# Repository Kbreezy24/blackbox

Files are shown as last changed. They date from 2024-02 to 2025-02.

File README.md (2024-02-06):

# Blackbox
Blackbox is an open source CoreXY tool-changing 3D Printer. Originally designed and open-sourced by Marc Schömann

Blackbox is a tool changing 3D Printer originally designed by Marc Schöemann to overcome the issue on properly integrating flexible materials with rigid materials for the production of flexible robotic appendages. The current revision of Blackbox was released as an open source project in 2017 and today we are happy to bring you the first of the Blackbox Family of tool changers - Blackbox CE (Community Edition). CE aims to accelerate the project through community participation and engagement via an accessible BOM and ease-of-assembly refinements.

# Is there a kit available for parts? 

Yes - Blackbox is supported by KB3D! Parts are available individually or as comprehensive kits. We continue to work with LDO Motors , Mandala Rose Works , and other trusted community vendors to expand your options.

# This machine looks intimidating, can I build one? 

Yes, but maybe. Blackbox has some new (to most) design elements that will push you to learn about systems you may not have dealt with before. In general though, the recommendations from other DIY printer build communities translate well. Those are typically as follows:<br />

This probably shouldn’t be your first 3D printer. There are always exceptions, but the experience you have will likely lean on your previously acquired skills from using and maintaining other machines. 
Despite our best efforts to guide you along, every machine will be different. From the quality of the printed parts to the nuances of your particular configuration. You should be comfortable with the fact that your attention to detail and where-with-all will determine the final product.
You will learn a ton, and probably pick up some new tools to make your life easier. Learning takes time, and so will your build. This is not an 8 hour build!

# Can I contribute, and how?
 
Absolutely! We encourage everyone to give back to the project however possible. Here are some ideas:

Sharing of modifications made to your machine that you think improve the experience or broaden the use case<br />
CAD optimization and contribution<br />
Bug fixes, error reporting, and feedback/suggestions<br />
Documentation refinement<br />
Help your peers where possible<br />
Purchasing parts through our official store at KB3D. 

# Features and Specs: 

# General: 
Blackbox is a fully open source design years in the making. Proven results over multiple iterations creates a solid foundation for a community driven machine limited only by our imaginations.

# Mechanical: 
Build Area = 300x300x275(Z)
Extremely Space efficient machine size vs build size when compared to other Tool Changers<br />
CoreXY Motion System = Intuitive belt routing with easy to use tensioning system.<br />
Belt Driven Z-Axis = Extremely fast belted Z axis with counterweight system.<br />
Tool-Changing = Up to 5 chassis mounted tools<br />
FDM = Up to 5 direct drive FDM tool heads with excellent positional accuracy via kinematic coupling. Support for multiple hot end configurations.<br />
Unique X-axis mounted extruder motor saves cost and complexity<br />
Silicone nozzle wiping and sealing<br />
Enclosure = Fully enclosed build volume (Hood Optional)<br />
REPRAP = Designed in the spirit of Reprap utilizing easily obtainable and 3D printable parts.<br />
Watercooling = Passive watercooling of all tools at all times in addition to a passively cooled extruder stepper<br />
Fully automated tool offset configuration using the late Danal Estes TAMV alignment system run from a Raspberry Pi.<br />
Heated Bed: Mains heated and ultra flat with options for embedded magnets

# Electronics: 
Wiring = Designed with clean and functional wiring in mind<br />
Duet 3 Electronics<br />
Automatic Bed Leveling and Z-Offset Calibration<br />
24V, 12V and 5V power sources for extreme flexibility<br />
Blackstop Hall Effect Sensors<br />
Tool lock position end stop - never drop a tool!

# Attributions:

Tool lock wedge plates are from the Jubilee Project https://github.com/machineagency/jubilee<br />
Heated Bed is from the Voron Project https://github.com/VoronDesign/Voron-2

All files are released according to the following license unless specified differently in the file or directory: CERN-OHL-W: https://ohwr.org/project/cernohl/wikis/Documents/CERN-OHL-version-2

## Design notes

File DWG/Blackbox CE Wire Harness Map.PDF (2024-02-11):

Main Harness Name | WIRE Name | Component A | Connector A | Component B | Connector B | Length Wire Gauge Color Marker Motion? Connector Name

Power Inlet
| Jumper - Line | Power Inlet | Female Spade | Power Switch | Female Spade | 8CM | 18 BLK | N
| Jumper - Neutral | Power Inlet | Female Spade | Power Switch | Female Spade | 8CM | 18 WHT | N
| Line Wire | Power Switch | Female Spade | 24V Power Supply | Fork | 20CM | 18 BLK | N
| Neutral Wire | Power Switch | Female Spade | 24V Power Supply | Fork | 20CM | 18 WHT | N
| Ground Wire | Power Inlet | Female Spade | 24V Power Supply | Fork | 20CM | 18 GN/YEL | N
Solid State Relay
| Line Wire (IN) | 24V Power Supply | Fork | SSR | Fork | 57CM | 18 BLK | N
| LINE Wire (LOAD) | SSR | Fork | Heated Bed WAGO | Bare Wire? | 86CM | 18 BLK | Y
| Trigger + | Duet 3 6HC | Molex LG Pin 2 of 2 | SSR IN + | Fork | 42CM | 24 RED | N | OUT_3
| Trigger - | Duet 3 6HC | Molex LG Pin 1 of 2 | SSR IN - | Fork | 42CM | 24 BLK | N | OUT_3

Heated Bed WAGOs
| Neutral 120V Wire | 24V Power Supply | Fork | Heated Bed WAGO | Bare Wire? | 133CM | 18 WHT | Y
| Bed Thermistor + | Duet 3 6HC | Molex KK Pin 2 of 2 | Heated Bed WAGO | Bare Wire? | 118CM | 24 RED | Y | TEMP_3
| Bed Thermistor - | Duet 3 6HC | Molex KK Pin 1 of 2 | Heated Bed WAGO | Bare Wire? | 118CM | 24 BLK | Y | TEMP_3

SexBolt Offset Switch
Switch S | Sexbolt Switch | JST-XH Pin 1 of 2 | Duet 3 6HC | Molex KK Pin 4 of 5 | 141CM | 24 GREEN | Y | IO_5
Switch - | Sexbolt Switch | JST-XH Pin 2 of 2 | Duet 3 6HC | Molex KK Pin 3 of 5 | 141CM | 24 BLK | Y | IO_5
12V DC Converter
| 24V IN + | 24V Power Supply | Fork | 12V Converter | Fork | 67CM | 18 RED | N
| 24V IN - | 24V Power Supply | Fork | 12V Converter | Fork | 67CM | 18 BLK | N

5V DC Converter
| 24V IN + | 24V Power Supply | Fork | 12V Converter | Fork | 74CM | 18 RED | N
| 24V IN - | 24V Power Supply | Fork | 12V Converter | Fork | 74CM | 18 BLK | N
| 5V Out + | 5V Converter | Fork | Duet 3 6HC | Molex KK PIN 3 of 3 | 60CM | 20 RED | N | 5V_EXT
| 5V OUT - | 5V Converter | Fork | Duet 3 6HC | Molex KK Pin 1 of 3 | 60CM | 20 BLK | N | 5V_EXT

Duet 3 6HC
| 24V IN + | 24V Power Supply | Fork | Duet 3 6HC | Fork | 91CM | 18 RED | N | POWER_IN
| 24V IN - | 24V Power Supply | Fork | Duet 3 6HC | Fork | 91CM | 18 BLACK | N | POWER_IN

Duet 3 3HC
| 24V IN + | Duet 3 6HC | Fork | Duet 3 3HC | Fork | 39CM | 18 RED | N | POWER_IN
| 24V IN - | Duet 3 6HC | Fork | Duet 3 3HC | Fork | 39CM | 18 BLACK | N | POWER_IN

Water Pump
| Radiator Fan + | Duet 3 6HC | Molex KK Pin 2 of 2 | 6020 Fan | Microfit Receptacle Pin 1 of 4 | 50CM | 24 RED | N | OUT_9
| Radiator Fan - | Duet 3 6HC | Molex KK Pin 1 of 2 | 6020 Fan | Microfit Receptacle Pin 2 of 4 | 50CM | 24 BLK | N | OUT_9
| 12V Out + | 12V Converter | Fork | Water Pump + | Microfit Receptacle Pin 3 of 4 | 86CM | 20 RED | N
| 12V OUT - | 12V Converter | Fork | Water Pump - | Microfit Receptacle Pin 4 of 4 | 86CM | 20 BLK | N

Display
| Display Data 1 | Duet 3 6HC | Molex KK Pin 1 of 5 | PanelDue | Molex KK Pin 1 of 4 | 62CM | 24 RED | N | IO_0
| Display Data 2 | Duet 3 6HC | Molex KK Pin 2 of 5 | PanelDue | Molex KK Pin 4 of 4 | 62CM | 24 GREEN | N | IO_0
| Display Data 3 | Duet 3 6HC | Molex KK Pin 3 of 5 | PanelDue | Molex KK Pin 2 of 4 | 62CM | 24 BLACK | N | IO_0
| Display Data 4 | Duet 3 6HC | Molex KK Pin 4 of 5 | PanelDue | Molex KK Pin 3 of 4 | 62CM | 24 BLUE | N | IO_0

Tool Docks
| Tool 0 Heater + | Duet 3 6HC | Molex LG Pin 2 of 2 | Tool Dock 0 | Microfit Receptacle Pin 4 of 4 | 136CM | 20 RED | N | OUT_1
| Tool 0 Heater - | Duet 3 6HC | Molex LG Pin 1 of 2 | Tool Dock 0 | Microfit Receptacle Pin 1 of 4 | 136CM | 20 BLACK | N | OUT_1
| Tool 0 Thermistor + | Duet 3 6HC | Molex KK Pin 1 of 2 | Tool Dock 0 | Microfit Receptacle Pin 2 of 4 | 136CM | 24 RED | N | TEMP_0
| Tool 0 Thermistor - | Duet 3 6HC | Molex KK Pin 2 of 2 | Tool Dock 0 | Microfit Receptacle Pin 3 of 4 | 136CM | 24 BLACK | N | TEMP_0
| Tool 1 Heater + | Duet 3 6HC | Molex LG Pin 2 of 2 | Tool Dock 1 | Microfit Receptacle Pin 4 of 4 | 141CM | 20 RED | N | OUT_2
| Tool 1 Heater - | Duet 3 6HC | Molex LG Pin 1 of 2 | Tool Dock 1 | Microfit Receptacle Pin 1 of 4 | 141CM | 20 BLACK | N | OUT_2
| Tool 1 Thermistor + | Duet 3 6HC | Molex KK Pin 1 of 2 | Tool Dock 1 | Microfit Receptacle Pin 2 of 4 | 141CM | 24 RED | N | TEMP_1
| Tool 1 Thermistor - | Duet 3 6HC | Molex KK Pin 2 of 2 | Tool Dock 1 | Microfit Receptacle Pin 3 of 4 | 141CM | 24 BLACK | N | TEMP_1
| Tool 2 Heater + | Duet 3 3HC | Molex LG Pin 2 of 2 | Tool Dock 2 | Microfit Receptacle Pin 4 of 4 | 131CM | 20 RED | N | OUT_0
| Tool 2 Heater - | Duet 3 3HC | Molex LG Pin 1 of 2 | Tool Dock 2 | Microfit Receptacle Pin 1 of 4 | 131CM | 20 BLACK | N | OUT_0
| Tool 2 Thermistor + | Duet 3 3HC | Molex KK Pin 1 of 2 | Tool Dock 2 | Microfit Receptacle Pin 2 of 4 | 131CM | 24 RED | N | TEMP_0
| Tool 2 Thermistor - | Duet 3 3HC | Molex KK Pin 2 of 2 | Tool Dock 2 | Microfit Receptacle Pin 3 of 4 | 131CM | 24 BLACK | N | TEMP_0
| Tool 3 Heater + | Duet 3 3HC | Molex LG Pin 2 of 2 | Tool Dock 3 | Microfit Receptacle Pin 4 of 4 | 136CM | 20 RED | N | OUT_1
| Tool 3 Heater - | Duet 3 3HC | Molex LG Pin 1 of 2 | Tool Dock 3 | Microfit Receptacle Pin 1 of 4 | 136CM | 20 BLACK | N | OUT_1
| Tool 3 Thermistor + | Duet 3 3HC | Molex KK Pin 1 of 2 | Tool Dock 3 | Microfit Receptacle Pin 2 of 4 | 136CM | 24 RED | N | TEMP_1
| Tool 3 Thermistor - | Duet 3 3HC | Molex KK Pin 2 of 2 | Tool Dock 3 | Microfit Receptacle Pin 3 of 4 | 136CM | 24 BLACK | N | TEMP_1
| Tool 4 Heater + | Duet 3 3HC | Molex LG Pin 2 of 2 | Tool Dock 4 | Microfit Receptacle Pin 4 of 4 | 141CM | 20 RED | N | OUT_2
| Tool 4 Heater - | Duet 3 3HC | Molex LG Pin 1 of 2 | Tool Dock 4 | Microfit Receptacle Pin 1 of 4 | 141CM | 20 BLACK | N | OUT_2
| Tool 4 Thermistor + | Duet 3 3HC | Molex KK Pin 1 of 2 | Tool Dock 4 | Microfit Receptacle Pin 2 of 4 | 141CM | 24 RED | N | TEMP_2
| Tool 4 Thermistor - | Duet 3 3HC | Molex KK Pin 2 of 2 | Tool Dock 4 | Microfit Receptacle Pin 3 of 4 | 141CM | 24 BLACK | N | TEMP_2
Enclosure Lighting | LED + (Stick1) | Duet 3 6HC | Molex KK Pin 2 of 2 | Light Stick 1 | JST XH Pin 2 of 2 | 144CM | 20 RED | N | OUT_8
| LED - (Stick1) | Duet 3 6HC | Molex KK Pin 1 of 2 | Light Stick 1 | JST XH Pin 1 of 2 | 144CM | 20 BLACK | N | OUT_8
| LED + (Stick2) | Light Stick 1 | JST XH Pin 2 of 2 | Light Stick 2 | JST XH Pin 2 of 2 | 16CM | 20 RED | N
| LED - (Stick2) | Light Stick 1 | JST XH Pin 1 of 2 | Light Stick 2 | JST XH Pin 1 of 2 | 16CM | 20 BLACK | N
| LED + (Stick3) | Light Stick 2 | JST XH Pin 2 of 2 | Light Stick 3 | JST XH Pin 2 of 2 | 16CM | 20 RED | N
| LED - (Stick3) | Light Stick 2 | JST XH Pin 1 of 2 | Light Stick 3 | JST XH Pin 1 of 2 | 16CM | 20 BLACK | N

FDM Tools

| Tool 0 Heater + | Tool Dock 0 | Microfit Receptacle Pin 4 of 4 | Tool Heater + | Microfit Receptacle Pin 1 of 2 | 70CM | 20 RED | Y
| Tool 0 Heater - | Tool Dock 0 | Microfit Receptacle Pin 1 of 4 | Tool Heater - | Microfit Receptacle Pin 2 of 2 | 70CM | 20 BLACK | Y
| Tool 0 Thermistor + | Tool Dock 0 | Microfit Receptacle Pin 2 of 4 | Tool Thermistor + | Microfit Receptacle Pin 1 of 2 | 72CM | 24 RED | Y
| Tool 0 Thermistor - | Tool Dock 0 | Microfit Receptacle Pin 3 of 4 | Tool Thermistor - | Microfit Receptacle Pin 2 of 2 | 72CM | 24 BLACK | Y

TOOL HEAD
| E Motor Pair 1 | Duet 3 6HC | Molex LG Pin 1 of 4 | Extruder Motor | JST PH Pin 1 of 6 | 256CM | 24 RED | Y | DRIVER_3

# BLACKBOX CE WIRE HARNESS MAP

E Motor Pair 1 | Duet 3 6HC | Molex LG Pin 2 of 4 | Extruder Motor | JST PH Pin 3 of 6 | 256CM | 24 BLUE | Y | DRIVER_3
E Motor Pair 2 | Duet 3 6HC | Molex LG Pin 3 of 4 | Extruder Motor | JST PH Pin 4 of 6 | 256CM | 24 GREEN | Y | DRIVER_3
E Motor Pair 2 | Duet 3 6HC | Molex LG Pin 4 of 4 | Extruder Motor | JST PH Pin 6 of 6 | 256CM | 24 BLACK | Y | DRIVER_3
T Motor Pair 1 | Duet 3 6HC | Molex LG Pin 1 of 4 | Tool Lock Motor | Microfit Connector Pin 1 of 4 | 256CM | 24 RED | Y | DRIVER_4
T Motor Pair 1 | Duet 3 6HC | Molex LG Pin 2 of 4 | Tool Lock Motor | Microfit Connector Pin 2 of 4 | 256CM | 24 BLUE | Y | DRIVER_4
T Motor Pair 2 | Duet 3 6HC | Molex LG Pin 3 of 4 | Tool Lock Motor | Microfit Connector Pin 3 of 4 | 256CM | 24 GREEN | Y | DRIVER_4
T Motor Pair 2 | Duet 3 6HC | Molex LG Pin 4 of 4 | Tool Lock Motor | Microfit Connector Pin 4 of 4 | 256CM | 24 BLACK | Y | DRIVER_4
X Endstop + | Duet 3 6HC | Molex KK Pin 5 of 5 | X Endstop | JST XH Pin 1 of 3 | 256CM | 24 RED | Y | IO_1
X Endstop S | Duet 3 6HC | Molex KK Pin 4 of 5 | X Endstop | JST XH Pin 2 of 3 | 256CM | 24 GREEN | Y | IO_1
X Endstop - | Duet 3 6HC | Molex KK Pin 3 of 5 | X Endstop | JST XH Pin 3 of 3 | 256CM | 24 BLACK | Y | IO_1
Z Endstop S | Duet 3 6HC | Molex KK Pin 4 of 5 | Z Endstop | Microfit Connector Pin 1 of 2 | 256CM | 24 GREEN | Y | IO_3
Z Endstop - | Duet 3 6HC | Molex KK Pin 3 of 5 | Z Endstop | Microfit Connector Pin 2 of 2 | 256CM | 24 BLACK | Y | IO_3
TL Endstop + | Duet 3 6HC | Molex KK Pin 5 of 5 | Tool Lock Endstop | JST XH Pin 1 of 3 | 256CM | 24 RED | Y | IO_4
TL Endstop S | Duet 3 6HC | Molex KK Pin 4 of 5 | Tool Lock Endstop | JST XH Pin 2 of 3 | 256CM | 24 GREEN | Y | IO_4
TL Endstop - | Duet 3 6HC | Molex KK Pin 3 of 5 | Tool Lock Endstop | JST XH Pin 3 of 3 | 256CM | 24 BLACK | Y | IO_4
Part Fan + | Duet 3 6HC | Molex KK Pin 2 of 2 | Part cooling Fan | Microfit Connector Pin 1 of 2 | 256CM | 24 RED | Y | OUT_7
Part Fan - | Duet 3 6HC | Molex KK Pin 1 of 2 | Part cooling Fan | Microfit Connector Pin 2 of 2 | 256CM | 24 BLACK | Y | OUT_7

Y Endstop

Y Endstop + | Duet 3 6HC | Molex KK Pin 5 of 5 | Y Endstop | JST XH Pin 1 of 3 | 83CM | 24 RED | N | IO_2
Y Endstop S | Duet 3 6HC | Molex KK Pin 4 of 5 | Y Endstop | JST XH Pin 2 of 3 | 83CM | 24 GREEN | N | IO_2
Y Endstop - | Duet 3 6HC | Molex KK Pin 3 of 5 | Y Endstop | JST XH Pin 3 of 3 | 83CM | 24 BLACK | N | IO_2

B Motor
B Motor Pair 1 | Duet 3 6HC | Molex LG Pin 1 of 4 | B Motor | JST PH Pin 1 of 6 | 61CM | 24 RED | N | DRIVER_0
B Motor Pair 1 | Duet 3 6HC | Molex LG Pin 2 of 4 | B Motor | JST PH Pin 3 of 6 | 61CM | 24 BLUE | N | DRIVER_0
B Motor Pair 2 | Duet 3 6HC | Molex LG Pin 3 of 4 | B Motor | JST PH Pin 4 of 6 | 61CM | 24 GREEN | N | DRIVER_0
B Motor Pair 2 | Duet 3 6HC | Molex LG Pin 4 of 4 | B Motor | JST PH Pin 6 of 6 | 61CM | 24 BLACK | N | DRIVER_0

A Motor
A Motor Pair 1 | Duet 3 6HC | Molex LG Pin 1 of 4 | A Motor | JST PH Pin 1 of 6 | 173CM | 24 RED | N | DRIVER_1
A Motor Pair 1 | Duet 3 6HC | Molex LG Pin 2 of 4 | A Motor | JST PH Pin 3 of 6 | 173CM | 24 BLUE | N | DRIVER_1
A Motor Pair 2 | Duet 3 6HC | Molex LG Pin 3 of 4 | A Motor | JST PH Pin 4 of 6 | 173CM | 24 GREEN | N | DRIVER_1
A Motor Pair 2 | Duet 3 6HC | Molex LG Pin 4 of 4 | A Motor | JST PH Pin 6 of 6 | 173CM | 24 BLACK | N | DRIVER_1

Z Motor
Z Motor Pair 1 | Duet 3 6HC | Molex LG Pin 1 of 4 | Z Motor | JST PH Pin 1 of 6 | 17CM | 24 RED | N | DRIVER_2
Z Motor Pair 1 | Duet 3 6HC | Molex LG Pin 2 of 4 | Z Motor | JST PH Pin 3 of 6 | 17CM | 24 BLUE | N | DRIVER_2
Z Motor Pair 2 | Duet 3 6HC | Molex LG Pin 3 of 4 | Z Motor | JST PH Pin 4 of 6 | 17CM | 24 GREEN | N | DRIVER_2
Z Motor Pair 2 | Duet 3 6HC | Molex LG Pin 4 of 4 | Z Motor | JST PH Pin 6 of 6 | 17CM | 24 BLACK | N | DRIVER_2

Raspberry Pi
RPI 5V+ | 5V DC Converter | Fork | RPI | USB-C | 40CM | 20 RED | N
RPI 5V- | 5V DC Converter | Fork | RPI | USB-C | 40CM | 20 BLK | N

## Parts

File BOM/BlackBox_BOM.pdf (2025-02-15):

# Blackbox BOM Export - CE - 08/18/2024

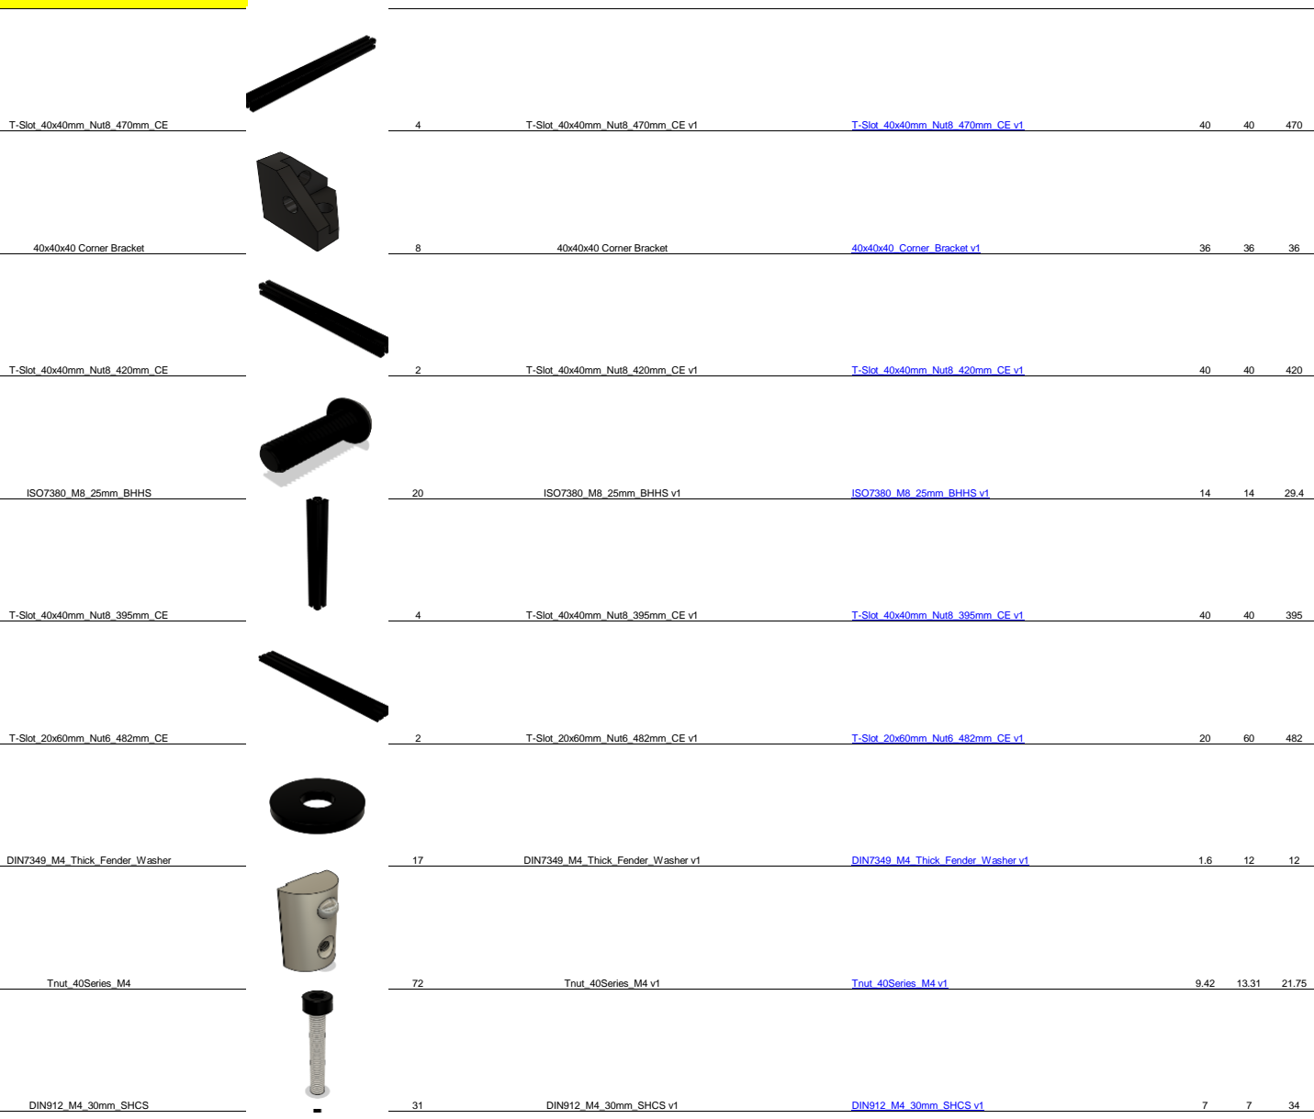
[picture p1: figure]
T-Slot_40x40mm_Nut8_470mm_CE; T-Slot_40x40mm_Nut8_470mm_CE v1; 40x40x40 Corner Bracket; 40x40x40_Corner_Bracket v1; T-Slot_40x40mm_Nut8_420mm_CE; T-Slot_40x40mm_Nut8_420mm_CE v1; ISO7380_M8_25mm_BHHS; ISO7380_M8_25mm_BHHS v1; T-Slot_40x40mm_Nut8_395mm_CE; T-Slot_40x40mm_Nut8_395mm_CE v1; T-Slot_20x60mm_Nut6_482mm_CE; T-Slot_20x60mm_Nut6_482mm_CE v1; DIN7349_M4_Thick_Fender_Washer; DIN7349_M4_Thick_Fender_Washer v1; Tnut_40Series_M4; Tnut_40Series_M4 v1; DIN912_M4_30mm_SHCS; DIN912_M4_30mm_SHCS v1

LinearRail_MGN12_335mm_LDO | 3 | LinearRail_MGN12_335mm_LDO v1 | LinearRail_MGN12_335mm_LDO v1 (https://gmail2024038.autodesk360.com/g/projects/20231224713178051/data/dXJuOmFkc2sud2lwcHJvZDpmcy5mb2xkZXI6Y28uMGxIVWluVGVSWTZtS2JGWFVKeEJkZw==/dXJuOmFkc2sud2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) | 8 | 12 | 335
Tnut_40Series_M3 | 36 | Tnut_40Series_M3 v1 | Tnut_40Series_M3 v1 (https://gmail2024038.autodesk360.com/g/projects/20231224713178051/data/dXJuOmFkc2sud2lwcHJvZDpmcy5mb2xkZXI6Y28uTktyRXlNMm5UcXFDbTlDbkJDRjZGQQ==/dXJuOmFkc2sud2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) | 9.42 | 13.31 | 21.75
DIN912_M3_14mm_SHCS | 44 | DIN912_M3_14mm_SHCS v1 | DIN912_M3_14mm_SHCS v1 (https://gmail2024038.autodesk360.com/g/projects/20231224713178051/data/dXJuOmFkc2sud2lwcHJvZDpmcy5mb2xkZXI6Y28uTktyRXlNMm5UcXFDbTlDbkJDRjZGQQ==/dXJuOmFkc2sud2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) | 5.5 | 5.5 | 17
LinearRail_MGN12_400mm_LDO | 2 | LinearRail_MGN12_400mm_LDO v1 | LinearRail_MGN12_400mm_LDO v1 (https://gmail2024038.autodesk360.com/g/projects/20231224713178051/data/dXJuOmFkc2sud2lwcHJvZDpmcy5mb2xkZXI6Y28uMGxIVWluVGVSWTZtS2JGWFVKeEJkZw==/dXJuOmFkc2sud2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) | 8 | 12 | 400
T-Slot_20x20mm_Nut6_395mm_CE | 1 | T-Slot_20x20mm_Nut6_395mm_CE v1 | T-Slot_20x20mm_Nut6_395mm_CE v1 (https://gmail2024038.autodesk360.com/g/projects/20231224713178051/data/dXJuOmFkc2sud2lwcHJvZDpmcy5mb2xkZXI6Y28uMGxIVWluVGVSWTZtS2JGWFVKeEJkZw==/dXJuOmFkc2sud2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) | 20 | 20 | 395
M4 20 Series T-Nut | 71 | M4 20 Series T-Nut | Tnut_20Series_M4 v1 (https://gmail2024038.autodesk360.com/g/projects/20231224713178051/data/dXJuOmFkc2sud2lwcHJvZDpmcy5mb2xkZXI6Y28uTktyRXlNMm5UcXFDbTlDbkJDRjZGQQ==/dXJuOmFkc2sud2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) | 4.3 | 7.709 | 12
DIN912_M4_16mm_SHCS | 6 | DIN912_M4_16mm_SHCS v1 | DIN912_M4_16mm_SHCS v1 (https://gmail2024038.autodesk360.com/g/projects/20231224713178051/data/dXJuOmFkc2sud2lwcHJvZDpmcy5mb2xkZXI6Y28uTktyRXlNMm5UcXFDbTlDbkJDRjZGQQ==/dXJuOmFkc2sud2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) | 7 | 7 | 20
DIN912_M4_35mm_SHCS | 14 | DIN912_M4_35mm_SHCS v1 | DIN912_M4_35mm_SHCS v1 (https://gmail2024038.autodesk360.com/g/projects/20231224713178051/data/dXJuOmFkc2sud2lwcHJvZDpmcy5mb2xkZXI6Y28uTktyRXlNMm5UcXFDbTlDbkJDRjZGQQ==/dXJuOmFkc2sud2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) | 7 | 7 | 39
M3 20 Series Roll-in Nut | 31 | M3 20 Series Roll-in Nut | Tnut_20Series_M3 v1 (https://gmail2024038.autodesk360.com/g/projects/20231224713178051/data/dXJuOmFkc2sud2lwcHJvZDpmcy5mb2xkZXI6Y28uTktyRXlNMm5UcXFDbTlDbkJDRjZGQQ==/dXJuOmFkc2sud2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) | 4.3 | 7.709 | 12

DIN912_M3_8mm_SHCS | 47 | DIN912_M3_8mm_SHCS v1 | DIN912_M3_8mm_SHCS v1 (https://gmail2024038.autodesk360.com/g/projects/20231224713178051/data/dXJuOmFkc2sud2lwcHJvZDpmcy5mb2xkZXI6Y28uTktyRXlNMm5UcXFDbTlDbkJDRjZGQQ==/dXJuOmFkc2sud2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) | 5.5 | 5.5 | 11
M3_4.6x4mm_Heat_Set_Insert | 173 | M3_4.6x4mm_Heat_Set_Insert v1 | M3_4.6x4mm_Heat_Set_Insert v1 (https://gmail2024038.autodesk360.com/g/projects/20231224713178051/data/dXJuOmFkc2sud2lwcHJvZDpmcy5mb2xkZXI6Y28uTktyRXlNMm5UcXFDbTlDbkJDRjZGQQ==/dXJuOmFkc2sud2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) | 4.3 | 4.7 | 4.7
DIN912_M3_10mm_SHCS | 36 | DIN912_M3_10mm_SHCS v1 | DIN912_M3_10mm_SHCS v1 (https://gmail2024038.autodesk360.com/g/projects/20231224713178051/data/dXJuOmFkc2sud2lwcHJvZDpmcy5mb2xkZXI6Y28uTktyRXlNMm5UcXFDbTlDbkJDRjZGQQ==/dXJuOmFkc2sud2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) | 5.5 | 5.5 | 13
M4_6x5mm_Heat_Set_Insert | 59 | M4_6x5mm_Heat_Set_Insert v1 | M4_6x5mm_Heat_Set_Insert v1 (https://gmail2024038.autodesk360.com/g/projects/20231224713178051/data/dXJuOmFkc2sud2lwcHJvZDpmcy5mb2xkZXI6Y28uTktyRXlNMm5UcXFDbTlDbkJDRjZGQQ==/dXJuOmFkc2sud2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) | 4.7 | 6.3 | 6.3
DIN7991_M4_25mm_FHHS | 8 | DIN7991_M4_25mm_FHHS v1 | DIN7991_M4_25mm_FHHS v1 (https://gmail2024038.autodesk360.com/g/projects/20231224713178051/data/dXJuOmFkc2sud2lwcHJvZDpmcy5mb2xkZXI6Y28uTktyRXlNMm5UcXFDbTlDbkJDRjZGQQ==/dXJuOmFkc2sud2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) | 8 | 8 | 25
Bearing_Flanged_5x10x4mm | 4 | Bearing_Flanged_5x10x4mm v1 | Bearing_Flanged_5x10x4mm v1 (https://gmail2024038.autodesk360.com/g/projects/20231224713178051/data/dXJuOmFkc2sud2lwcHJvZDpmcy5mb2xkZXI6Y28uMGxIVWluVGVSWTZtS2JGWFVKeEJkZw==/dXJuOmFkc2sud2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) | 4 | 11.6 | 11.6
GT2_40t_Pulley_9mm_Belt_5mm_Bore_Powge | 1 | GT2_40t_Pulley_9mm_Belt_5mm_Bore_Powge v1 | GT2_40t_Pulley_9mm_Belt_5mm_Bore_Powge v1 (https://gmail2024038.autodesk360.com/g/projects/20231224713178051/data/dXJuOmFkc2sud2lwcHJvZDpmcy5mb2xkZXI6Y28uMGxIVWluVGVSWTZtS2JGWFVKeEJkZw==/dXJuOmFkc2sud2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) | 23 | 30 | 30
GT2_16t_Pulley_9mm_Belt_5mm_Bore_Powge | 2 | GT2_16t_Pulley_9mm_Belt_5mm_Bore_Powge v1 | GT2_16t_Pulley_9mm_Belt_5mm_Bore_Powge v1 (https://gmail2024038.autodesk360.com/g/projects/20231224713178051/data/dXJuOmFkc2sud2lwcHJvZDpmcy5mb2xkZXI6Y28uMGxIVWluVGVSWTZtS2JGWFVKeEJkZw==/dXJuOmFkc2sud2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) | 14 | 14 | 21
Linear_Shaft_5x70mm | 1 | Linear_Shaft_5x70mm v1 | Linear_Shaft_5x70mm v1 (https://gmail2024038.autodesk360.com/g/projects/20231224713178051/data/dXJuOmFkc2sud2lwcHJvZDpmcy5mb2xkZXI6Y28uMGxIVWluVGVSWTZtS2JGWFVKeEJkZw==/dXJuOmFkc2sud2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) | 5 | 5 | 70

DIN916_M4_4mm_Set_Screw | 12 | DIN916_M4_4mm_Set_Screw v1 | DIN916_M4_4mm_Set_Screw v1 (https://gmail2024038.autodesk360.com/g/projects/20231224713178051/data/dXJuOmFkc2sud2lwcHJvZDpmcy5mb2xkZXI6Y28uTktyRXlNMm5UcXFDbTlDbkJDRjZGQQ==/dXJuOmFkc2sud2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) | 4 | 4 | 4.025
DIN916_M4_6mm_Set_Screw | 2 | DIN916_M4_6mm_Set_Screw v1 | DIN916_M4_6mm_Set_Screw v1 (https://gmail2024038.autodesk360.com/g/projects/20231224713178051/data/dXJuOmFkc2sud2lwcHJvZDpmcy5mb2xkZXI6Y28uTktyRXlNMm5UcXFDbTlDbkJDRjZGQQ==/dXJuOmFkc2sud2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) | 4 | 4.025 | 6
DIN912_M4_20mm_SHCS | 9 | DIN912_M4_20mm_SHCS v1 | DIN912_M4_20mm_SHCS v1 (https://gmail2024038.autodesk360.com/g/projects/20231224713178051/data/dXJuOmFkc2sud2lwcHJvZDpmcy5mb2xkZXI6Y28uTktyRXlNMm5UcXFDbTlDbkJDRjZGQQ==/dXJuOmFkc2sud2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) | 7 | 7 | 24
DIN912_M4_22mm_SHCS | 2 | DIN912_M4_22mm_SHCS v1 | DIN912_M4_22mm_SHCS v1 (https://gmail2024038.autodesk360.com/g/projects/20231224713178051/data/dXJuOmFkc2sud2lwcHJvZDpmcy5mb2xkZXI6Y28uTktyRXlNMm5UcXFDbTlDbkJDRjZGQQ==/dXJuOmFkc2sud2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) | 7 | 7 | 26
DIN912_M4_14mm_SHCS | 13 | DIN912_M4_14mm_SHCS v1 | DIN912_M4_14mm_SHCS v1 (https://gmail2024038.autodesk360.com/g/projects/20231224713178051/data/dXJuOmFkc2sud2lwcHJvZDpmcy5mb2xkZXI6Y28uTktyRXlNMm5UcXFDbTlDbkJDRjZGQQ==/dXJuOmFkc2sud2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) | 7 | 7 | 18
GT2_77t_Belt_9x154mm | 1 | GT2_77t_Belt_9x154mm v1 | GT2_77t_Belt_9x154mm v1 (https://gmail2024038.autodesk360.com/g/projects/20231224713178051/data/dXJuOmFkc2sud2lwcHJvZDpmcy5mb2xkZXI6Y28uMGxIVWluVGVSWTZtS2JGWFVKeEJkZw==/dXJuOmFkc2sud2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) | 9 | 26.217 | 66.973
Nema17_47mm | 3 | Nema17_47mm v1 | Nema17_47mm v1 (https://gmail2024038.autodesk360.com/g/projects/20231224713178051/data/dXJuOmFkc2sud2lwcHJvZDpmcy5mb2xkZXI6Y28uMGxIVWluVGVSWTZtS2JGWFVKeEJkZw==/dXJuOmFkc2sud2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) | 42 | 42 | 71.5
DIN912_M4_10mm_SHCS | 11 | DIN912_M4_10mm_SHCS v1 | DIN912_M4_10mm_SHCS v1 (https://gmail2024038.autodesk360.com/g/projects/20231224713178051/data/dXJuOmFkc2sud2lwcHJvZDpmcy5mb2xkZXI6Y28uTktyRXlNMm5UcXFDbTlDbkJDRjZGQQ==/dXJuOmFkc2sud2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) | 7 | 7 | 14
DIN912_M4_12mm_SHCS | 24 | DIN912_M4_12mm_SHCS v1 | DIN912_M4_12mm_SHCS v1 (https://gmail2024038.autodesk360.com/g/projects/20231224713178051/data/dXJuOmFkc2sud2lwcHJvZDpmcy5mb2xkZXI6Y28uTktyRXlNMm5UcXFDbTlDbkJDRjZGQQ==/dXJuOmFkc2sud2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) | 7 | 7 | 16

GT2_94t_Belt_9x188mm | 1 | GT2_94t_Belt_9x188mm v1 | GT2_94t_Belt_9x188mm v1 (https://gmail2024038.autodesk360.com/g/projects/20231224713178051/data/dXJuOmFkc2sud2lwcHJvZDpmcy5mb2xkZXI6Y28uMGxIVWluVGVSWTZtS2JGWFVKeEJkZw==/dXJuOmFkc2sud2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) | 9 | 51.682 | 72.109
GT2_80t_Pulley_9mm_Belt_8mm_Bore_Powge | 1 | GT2_80t_Pulley_9mm_Belt_8mm_Bore_Powge v1 | GT2_80t_Pulley_9mm_Belt_8mm_Bore_Powge v1 (https://gmail2024038.autodesk360.com/g/projects/20231224713178051/data/dXJuOmFkc2sud2lwcHJvZDpmcy5mb2xkZXI6Y28uMGxIVWluVGVSWTZtS2JGWFVKeEJkZw==/dXJuOmFkc2sud2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) | 23 | 54 | 54
DIN916_M5_12mm_Set_Screw | 2 | DIN916_M5_12mm_Set_Screw v1 | DIN916_M5_12mm_Set_Screw v1 (https://gmail2024038.autodesk360.com/g/projects/20231224713178051/data/dXJuOmFkc2sud2lwcHJvZDpmcy5mb2xkZXI6Y28uTktyRXlNMm5UcXFDbTlDbkJDRjZGQQ==/dXJuOmFkc2sud2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) | 5 | 5.025 | 12
T-Slot_10x20mm_Nut6_350mm_CE | 1 | T-Slot_10x20mm_Nut6_350mm_CE v1 | T-Slot_10x20mm_Nut6_350mm_CE v1 (https://gmail2024038.autodesk360.com/g/projects/20231224713178051/data/dXJuOmFkc2sud2lwcHJvZDpmcy5mb2xkZXI6Y28uMGxIVWluVGVSWTZtS2JGWFVKeEJkZw==/dXJuOmFkc2sud2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) | 10 | 20 | 350
20x20_Corner_Bracket | 11 | 20x20_Corner_Bracket v1 | 20x20_Corner_Bracket v1 (https://gmail2024038.autodesk360.com/g/projects/20231224713178051/data/dXJuOmFkc2sud2lwcHJvZDpmcy5mb2xkZXI6Y28uMGxIVWluVGVSWTZtS2JGWFVKeEJkZw==/dXJuOmFkc2sud2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) | 19.8 | 19.8 | 19.8
DIN125_M4_Washer | 26 | DIN125_M4_Washer v1 | DIN125_M4_Washer v1 (https://gmail2024038.autodesk360.com/g/projects/20231224713178051/data/dXJuOmFkc2sud2lwcHJvZDpmcy5mb2xkZXI6Y28uTktyRXlNMm5UcXFDbTlDbkJDRjZGQQ==/dXJuOmFkc2sud2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) | 0.8 | 9 | 9
ISO7380_M4_8mm_BHHS | 38 | ISO7380_M4_8mm_BHHS v1 | ISO7380_M4_8mm_BHHS v1 (https://gmail2024038.autodesk360.com/g/projects/20231224713178051/data/dXJuOmFkc2sud2lwcHJvZDpmcy5mb2xkZXI6Y28uTktyRXlNMm5UcXFDbTlDbkJDRjZGQQ==/dXJuOmFkc2sud2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) | 7.6 | 7.6 | 10.2
Linear_Shaft_8x520mm | 1 | Linear_Shaft_8x520mm v1 | Linear_Shaft_8x520mm v1 (https://gmail2024038.autodesk360.com/g/projects/20231224713178051/data/dXJuOmFkc2sud2lwcHJvZDpmcy5mb2xkZXI6Y28uMGxIVWluVGVSWTZtS2JGWFVKeEJkZw==/dXJuOmFkc2sud2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) | 8 | 8 | 520
DIN912_M4_45mm_SHCS | 2 | DIN912_M4_45mm_SHCS v1 | DIN912_M4_45mm_SHCS v1 (https://gmail2024038.autodesk360.com/g/projects/20231224713178051/data/dXJuOmFkc2sud2lwcHJvZDpmcy5mb2xkZXI6Y28uTktyRXlNMm5UcXFDbTlDbkJDRjZGQQ==/dXJuOmFkc2sud2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) | 7 | 7 | 49

GT2_40t_Pulley_9mm_Belt_8mm_Bore_Powge | 2 | GT2_40t_Pulley_9mm_Belt_8mm_Bore_Powge v1 | GT2_40t_Pulley_9mm_Belt_8mm_Bore_Powge v1 (https://gmail2024038.autodesk360.com/g/projects/20231224713178051/data/dXJuOmFkc2sud2lwcHJvZDpmcy5mb2xkZXI6Y28uMGxIVWluVGVSWTZtS2JGWFVKeEJkZw==/dXJuOmFkc2sud2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) | 23 | 30 | 30
Bearing_5x9x3mm | 28 | Bearing_5x9x3mm v1 | Bearing_5x9x3mm v1 (https://gmail2024038.autodesk360.com/g/projects/20231224713178051/data/dXJuOmFkc2sud2lwcHJvZDpmcy5mb2xkZXI6Y28uMGxIVWluVGVSWTZtS2JGWFVKeEJkZw==/dXJuOmFkc2sud2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) | 3 | 9 | 9
Linear_Shaft_5x25mm | 4 | Linear_Shaft_5x25mm v1 | Linear_Shaft_5x25mm v1 (https://gmail2024038.autodesk360.com/g/projects/20231224713178051/data/dXJuOmFkc2sud2lwcHJvZDpmcy5mb2xkZXI6Y28uMGxIVWluVGVSWTZtS2JGWFVKeEJkZw==/dXJuOmFkc2sud2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) | 5 | 5 | 25
DIN916_M3_5mm_Set_Screw | 19 | DIN916_M3_5mm_Set_Screw v1 | DIN916_M3_5mm_Set_Screw v1 (https://gmail2024038.autodesk360.com/g/projects/20231224713178051/data/dXJuOmFkc2sud2lwcHJvZDpmcy5mb2xkZXI6Y28uTktyRXlNMm5UcXFDbTlDbkJDRjZGQQ==/dXJuOmFkc2sud2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) | 2.927 | 2.927 | 5
DIN916_M3_6mm_Set_Screw | 21 | DIN916_M3_6mm_Set_Screw v1 | DIN916_M3_6mm_Set_Screw v1 (https://gmail2024038.autodesk360.com/g/projects/20231224713178051/data/dXJuOmFkc2sud2lwcHJvZDpmcy5mb2xkZXI6Y28uTktyRXlNMm5UcXFDbTlDbkJDRjZGQQ==/dXJuOmFkc2sud2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) | 2.927 | 2.927 | 6
Bearing_4x9x4mm | 8 | Bearing_4x9x4mm v1 | Bearing_4x9x4mm v1 (https://gmail2024038.autodesk360.com/g/projects/20231224713178051/data/dXJuOmFkc2sud2lwcHJvZDpmcy5mb2xkZXI6Y28uMGxIVWluVGVSWTZtS2JGWFVKeEJkZw==/dXJuOmFkc2sud2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) | 4 | 9 | 9
T-Slot_20x40mm_Nut6_470.5mm_CE | 2 | T-Slot_20x40mm_Nut6_470.5mm_CE v1 | T-Slot_20x40mm_Nut6_470.5mm_CE v1 (https://gmail2024038.autodesk360.com/g/projects/20231224713178051/data/dXJuOmFkc2sud2lwcHJvZDpmcy5mb2xkZXI6Y28uMGxIVWluVGVSWTZtS2JGWFVKeEJkZw==/dXJuOmFkc2sud2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) | 20 | 40 | 470.5
T-Slot_20x40mm_Nut6_373mm_CE | 2 | T-Slot_20x40mm_Nut6_373mm_CE v1 | T-Slot_20x40mm_Nut6_373mm_CE v1 (https://gmail2024038.autodesk360.com/g/projects/20231224713178051/data/dXJuOmFkc2sud2lwcHJvZDpmcy5mb2xkZXI6Y28uMGxIVWluVGVSWTZtS2JGWFVKeEJkZw==/dXJuOmFkc2sud2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) | 20 | 40 | 373
LinearCarriage_MGN12H_LDO | 6 | LinearCarriage_MGN12H_LDO v1 | LinearCarriage_MGN12H_LDO v1 (https://gmail2024038.autodesk360.com/g/projects/20231224713178051/data/dXJuOmFkc2sud2lwcHJvZDpmcy5mb2xkZXI6Y28uMGxIVWluVGVSWTZtS2JGWFVKeEJkZw==/dXJuOmFkc2sud2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) | 10 | 27 | 45.4

DIN912_M3_35mm_SHCS | 5 | DIN912_M3_35mm_SHCS v1 | DIN912_M3_35mm_SHCS v1 (https://gmail2024038.autodesk360.com/g/projects/20231224713178051/data/dXJuOmFkc2sud2lwcHJvZDpmcy5mb2xkZXI6Y28uTktyRXlNMm5UcXFDbTlDbkJDRjZGQQ==/dXJuOmFkc2sud2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) | 5.5 | 5.5 | 38
DIN912_M4_6mm_SHCS | 26 | DIN912_M4_6mm_SHCS v1 | DIN912_M4_6mm_SHCS v1 (https://gmail2024038.autodesk360.com/g/projects/20231224713178051/data/dXJuOmFkc2sud2lwcHJvZDpmcy5mb2xkZXI6Y28uTktyRXlNMm5UcXFDbTlDbkJDRjZGQQ==/dXJuOmFkc2sud2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) | 7 | 7 | 10
DIN912_M4_40mm_SHCS | 4 | DIN912_M4_40mm_SHCS v1 | DIN912_M4_40mm_SHCS v1 (https://gmail2024038.autodesk360.com/g/projects/20231224713178051/data/dXJuOmFkc2sud2lwcHJvZDpmcy5mb2xkZXI6Y28uTktyRXlNMm5UcXFDbTlDbkJDRjZGQQ==/dXJuOmFkc2sud2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) | 7 | 7 | 44
DIN7991_M4_35mm_FHHS | 4 | DIN7991_M4_35mm_FHHS v1 | DIN7991_M4_35mm_FHHS v1 (https://gmail2024038.autodesk360.com/g/projects/20231224713178051/data/dXJuOmFkc2sud2lwcHJvZDpmcy5mb2xkZXI6Y28uTktyRXlNMm5UcXFDbTlDbkJDRjZGQQ==/dXJuOmFkc2sud2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) | 8 | 8 | 35
DIN912_M3_50mm_SHCS | 12 | DIN912_M3_50mm_SHCS v1 | DIN912_M3_50mm_SHCS v1 (https://gmail2024038.autodesk360.com/g/projects/20231224713178051/data/dXJuOmFkc2sud2lwcHJvZDpmcy5mb2xkZXI6Y28uTktyRXlNMm5UcXFDbTlDbkJDRjZGQQ==/dXJuOmFkc2sud2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) | 5.5 | 5.5 | 53
T-Slot_20x20mm_Nut6_373mm_CE | 2 | T-Slot_20x20mm_Nut6_373mm_CE v1 | T-Slot_20x20mm_Nut6_373mm_CE v1 (https://gmail2024038.autodesk360.com/g/projects/20231224713178051/data/dXJuOmFkc2sud2lwcHJvZDpmcy5mb2xkZXI6Y28uMGxIVWluVGVSWTZtS2JGWFVKeEJkZw==/dXJuOmFkc2sud2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) | 20 | 20 | 373
T-Slot_20x20mm_Nut6_270mm_CE | 1 | T-Slot_20x20mm_Nut6_270mm_CE v1 | T-Slot_20x20mm_Nut6_270mm_CE v1 (https://gmail2024038.autodesk360.com/g/projects/20231224713178051/data/dXJuOmFkc2sud2lwcHJvZDpmcy5mb2xkZXI6Y28uMGxIVWluVGVSWTZtS2JGWFVKeEJkZw==/dXJuOmFkc2sud2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) | 20 | 20 | 270
GT2_434t_Belt_9x868mm_(1.52mm) | 2 | GT2_434t_Belt_9x868mm_(1.52mm) v1 | GT2_434t_Belt_9x868mm_(1.52mm) v1 (https://gmail2024038.autodesk360.com/g/projects/20231224713178051/data/dXJuOmFkc2sud2lwcHJvZDpmcy5mb2xkZXI6Y28uMGxIVWluVGVSWTZtS2JGWFVKeEJkZw==/dXJuOmFkc2sud2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) | 9 | 26.497 | 432.13
Matched_Height_Kinematics_MRW_CE | 1 | Matched_Height_Kinematics_MRW_CE v1 | Matched_Height_Kinematics_MRW_CE v1 (https://gmail2024038.autodesk360.com/g/projects/20231224713178051/data/dXJuOmFkc2sud2lwcHJvZDpmcy5mb2xkZXI6Y28uMGxIVWluVGVSWTZtS2JGWFVKeEJkZw==/dXJuOmFkc2sud2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) | 36.12 | 271.75 | 316.95

HeatBed_MRW_CE | 1 | HeatBed_MRW_CE v1 | HeatBed_MRW_CE v1 (https://gmail2024038.autodesk360.com/g/projects/20231224713178051/data/dXJuOmFkc2sud2lwcHJvZDpmcy5mb2xkZXI6Y28uMGxIVWluVGVSWTZtS2JGWFVKeEJkZw==/dXJuOmFkc2sud2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) | 6 | 304.8 | 304.8
Silicone_Heater_CE | 1 | Silicone_Heater_CE v1 | Silicone_Heater_CE v1 (https://gmail2024038.autodesk360.com/g/projects/20231224713178051/data/dXJuOmFkc2sud2lwcHJvZDpmcy5mb2xkZXI6Y28uMGxIVWluVGVSWTZtS2JGWFVKeEJkZw==/dXJuOmFkc2sud2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) | 1.5 | 295 | 295
Thermal_Fuse_135C | 1 | Thermal_Fuse_135C v1 | Thermal_Fuse_135C v1 (https://gmail2024038.autodesk360.com/g/projects/20231224713178051/data/dXJuOmFkc2sud2lwcHJvZDpmcy5mb2xkZXI6Y28uMGxIVWluVGVSWTZtS2JGWFVKeEJkZw==/dXJuOmFkc2sud2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) | 6 | 14 | 57
T-Slot_10x20mm_Nut6_488mm_CE | 1 | T-Slot_10x20mm_Nut6_488mm_CE v1 | T-Slot_10x20mm_Nut6_488mm_CE v1 (https://gmail2024038.autodesk360.com/g/projects/20231224713178051/data/dXJuOmFkc2sud2lwcHJvZDpmcy5mb2xkZXI6Y28uMGxIVWluVGVSWTZtS2JGWFVKeEJkZw==/dXJuOmFkc2sud2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) | 10 | 20 | 488
LinearRail_MGN12_375mm_LDO | 1 | LinearRail_MGN12_375mm_LDO v1 | LinearRail_MGN12_375mm_LDO v1 (https://gmail2024038.autodesk360.com/g/projects/20231224713178051/data/dXJuOmFkc2sud2lwcHJvZDpmcy5mb2xkZXI6Y28uMGxIVWluVGVSWTZtS2JGWFVKeEJkZw==/dXJuOmFkc2sud2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) | 8 | 12 | 375
Linear_Shaft_5x35mm | 4 | Linear_Shaft_5x35mm v1 | Linear_Shaft_5x35mm v1 (https://gmail2024038.autodesk360.com/g/projects/20231224713178051/data/dXJuOmFkc2sud2lwcHJvZDpmcy5mb2xkZXI6Y28uMGxIVWluVGVSWTZtS2JGWFVKeEJkZw==/dXJuOmFkc2sud2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) | 5 | 5 | 35
ISO7380_M4_30mm_BHHS | 2 | ISO7380_M4_30mm_BHHS v1 | ISO7380_M4_30mm_BHHS v1 (https://gmail2024038.autodesk360.com/g/projects/20231224713178051/data/dXJuOmFkc2sud2lwcHJvZDpmcy5mb2xkZXI6Y28uTktyRXlNMm5UcXFDbTlDbkJDRjZGQQ==/dXJuOmFkc2sud2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) | 7.6 | 7.6 | 32.2
DIN912_M3_40mm_SHCS | 9 | DIN912_M3_40mm_SHCS v1 | DIN912_M3_40mm_SHCS v1 (https://gmail2024038.autodesk360.com/g/projects/20231224713178051/data/dXJuOmFkc2sud2lwcHJvZDpmcy5mb2xkZXI6Y28uTktyRXlNMm5UcXFDbTlDbkJDRjZGQQ==/dXJuOmFkc2sud2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) | 5.5 | 5.5 | 43
DIN9021_M3_Fender_Washer | 22 | DIN9021_M3_Fender_Washer v1 | DIN9021_M3_Fender_Washer v1 (https://gmail2024038.autodesk360.com/g/projects/20231224713178051/data/dXJuOmFkc2sud2lwcHJvZDpmcy5mb2xkZXI6Y28uTktyRXlNMm5UcXFDbTlDbkJDRjZGQQ==/dXJuOmFkc2sud2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) | 0.8 | 9 | 9

Neodymium_Cylinder_Magnet_3x3mm | 2 | Neodymium_Cylinder_Magnet_3x3mm v1 | Neodymium_Cylinder_Magnet_3x3mm v1 (https://gmail2024038.autodesk360.com/g/projects/20231224713178051/data/dXJuOmFkc2sud2lwcHJvZDpmcy5mb2xkZXI6Y28uMGxIVWluVGVSWTZtS2JGWFVKeEJkZw==/dXJuOmFkc2sud2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) | 3 | 3 | 3
GT2_20t_Pulley_9mm_Belt_5mm_Bore | 2 | GT2_20t_Pulley_9mm_Belt_5mm_Bore v1 | GT2_20t_Pulley_9mm_Belt_5mm_Bore v1 (https://gmail2024038.autodesk360.com/g/projects/20231224713178051/data/dXJuOmFkc2sud2lwcHJvZDpmcy5mb2xkZXI6Y28uMGxIVWluVGVSWTZtS2JGWFVKeEJkZw==/dXJuOmFkc2sud2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) | 15 | 15 | 20
DIN912_M3_45mm_SHCS | 6 | DIN912_M3_45mm_SHCS v1 | DIN912_M3_45mm_SHCS v1 (https://gmail2024038.autodesk360.com/g/projects/20231224713178051/data/dXJuOmFkc2sud2lwcHJvZDpmcy5mb2xkZXI6Y28uTktyRXlNMm5UcXFDbTlDbkJDRjZGQQ==/dXJuOmFkc2sud2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) | 5.5 | 5.5 | 48
Linear_Shaft_5x30mm | 2 | Linear_Shaft_5x30mm v1 | Linear_Shaft_5x30mm v1 (https://gmail2024038.autodesk360.com/g/projects/20231224713178051/data/dXJuOmFkc2sud2lwcHJvZDpmcy5mb2xkZXI6Y28uMGxIVWluVGVSWTZtS2JGWFVKeEJkZw==/dXJuOmFkc2sud2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) | 5 | 5 | 30
ISO7380_M3_35mm_BHHS | 4 | ISO7380_M3_35mm_BHHS v1 | ISO7380_M3_35mm_BHHS v1 (https://gmail2024038.autodesk360.com/g/projects/20231224713178051/data/dXJuOmFkc2sud2lwcHJvZDpmcy5mb2xkZXI6Y28uTktyRXlNMm5UcXFDbTlDbkJDRjZGQQ==/dXJuOmFkc2sud2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) | 5.7 | 5.7 | 36.65
Linear_Shaft_5x50mm | 4 | Linear_Shaft_5x50mm v1 | Linear_Shaft_5x50mm v1 (https://gmail2024038.autodesk360.com/g/projects/20231224713178051/data/dXJuOmFkc2sud2lwcHJvZDpmcy5mb2xkZXI6Y28uMGxIVWluVGVSWTZtS2JGWFVKeEJkZw==/dXJuOmFkc2sud2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) | 5 | 5 | 50
DIN912_M3_25mm_SHCS | 9 | DIN912_M3_25mm_SHCS v1 | DIN912_M3_25mm_SHCS v1 (https://gmail2024038.autodesk360.com/g/projects/20231224713178051/data/dXJuOmFkc2sud2lwcHJvZDpmcy5mb2xkZXI6Y28uTktyRXlNMm5UcXFDbTlDbkJDRjZGQQ==/dXJuOmFkc2sud2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) | 5.5 | 5.5 | 28
Linear_Shaft_2x6mm | 2 | Linear_Shaft_2x6mm v1 | Linear_Shaft_2x6mm v1 (https://gmail2024038.autodesk360.com/g/projects/20231224713178051/data/dXJuOmFkc2sud2lwcHJvZDpmcy5mb2xkZXI6Y28uMGxIVWluVGVSWTZtS2JGWFVKeEJkZw==/dXJuOmFkc2sud2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) | 2 | 2 | 6
DIN912_M4_25mm_SHCS | 3 | DIN912_M4_25mm_SHCS v1 | DIN912_M4_25mm_SHCS v1 (https://gmail2024038.autodesk360.com/g/projects/20231224713178051/data/dXJuOmFkc2sud2lwcHJvZDpmcy5mb2xkZXI6Y28uTktyRXlNMm5UcXFDbTlDbkJDRjZGQQ==/dXJuOmFkc2sud2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) | 7 | 7 | 29

BlackStop | 3 | BlackStop v1 | BlackStop v1 (https://gmail2024038.autodesk360.com/g/projects/20231224713178051/data/dXJuOmFkc2sud2lwcHJvZDpmcy5mb2xkZXI6Y28uMGxIVWluVGVSWTZtS2JGWFVKeEJkZw==/dXJuOmFkc2sud2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) | 7.6 | 14 | 35
DIN912_M3_30mm_SHCS | 2 | DIN912_M3_30mm_SHCS v1 | DIN912_M3_30mm_SHCS v1 (https://gmail2024038.autodesk360.com/g/projects/20231224713178051/data/dXJuOmFkc2sud2lwcHJvZDpmcy5mb2xkZXI6Y28uTktyRXlNMm5UcXFDbTlDbkJDRjZGQQ==/dXJuOmFkc2sud2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) | 5.5 | 5.5 | 33
GT2_894t_Belt_9x1788mm_Rear_(1.52mm) | 1 | GT2_894t_Belt_9x1788mm_Rear_(1.52mm) v1 | GT2_894t_Belt_9x1788mm_Rear_(1.52mm) v1 (https://gmail2024038.autodesk360.com/g/projects/20231224713178051/data/dXJuOmFkc2sud2lwcHJvZDpmcy5mb2xkZXI6Y28uMGxIVWluVGVSWTZtS2JGWFVKeEJkZw==/dXJuOmFkc2sud2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) | 9 | 450.764 474.158
GT2_894t_Belt_9x1788mm_Front_(1.52mm) | 1 | GT2_894t_Belt_9x1788mm_Front_(1.52mm) v1 | GT2_894t_Belt_9x1788mm_Front_(1.52mm) v1 (https://gmail2024038.autodesk360.com/g/projects/20231224713178051/data/dXJuOmFkc2sud2lwcHJvZDpmcy5mb2xkZXI6Y28uMGxIVWluVGVSWTZtS2JGWFVKeEJkZw==/dXJuOmFkc2sud2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) | 9 | 450.764 474.158
CNC_X-Plate_Kelvin_External_Cooler_V2 | 1 | CNC_X-Plate_Kelvin_External_Cooler_V2 v1 | CNC_X-Plate_Kelvin_External_Cooler_V2 v1 (https://gmail2024038.autodesk360.com/g/projects/20231224713178051/data/dXJuOmFkc2sud2lwcHJvZDpmcy5mb2xkZXI6Y28uMGxIVWluVGVSWTZtS2JGWFVKeEJkZw==/dXJuOmFkc2sud2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) | 4 | 62.5 | 125
DIN7991_M3_6mm_FHHS | 23 | DIN7991_M3_6mm_FHHS v1 | DIN7991_M3_6mm_FHHS v1 (https://gmail2024038.autodesk360.com/g/projects/20231224713178051/data/dXJuOmFkc2sud2lwcHJvZDpmcy5mb2xkZXI6Y28uTktyRXlNMm5UcXFDbTlDbkJDRjZGQQ==/dXJuOmFkc2sud2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) | 6 | 6 | 6
Linear_Shaft_3x8mm | 5 | Linear_Shaft_3x8mm v1 | Linear_Shaft_3x8mm v1 (https://gmail2024038.autodesk360.com/g/projects/20231224713178051/data/dXJuOmFkc2sud2lwcHJvZDpmcy5mb2xkZXI6Y28uMGxIVWluVGVSWTZtS2JGWFVKeEJkZw==/dXJuOmFkc2sud2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) | 3 | 3 | 8
CNC_Belt_Clamp_Left | 2 | CNC_Belt_Clamp_Left v1 | CNC_Belt_Clamp_Left v1 (https://gmail2024038.autodesk360.com/g/projects/20231224713178051/data/dXJuOmFkc2sud2lwcHJvZDpmcy5mb2xkZXI6Y28uMGxIVWluVGVSWTZtS2JGWFVKeEJkZw==/dXJuOmFkc2sud2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) | 4 | 7 | 27.4
ISO7380_M3_8mm_BHHS | 12 | ISO7380_M3_8mm_BHHS v1 | ISO7380_M3_8mm_BHHS v1 (https://gmail2024038.autodesk360.com/g/projects/20231224713178051/data/dXJuOmFkc2sud2lwcHJvZDpmcy5mb2xkZXI6Y28uTktyRXlNMm5UcXFDbTlDbkJDRjZGQQ==/dXJuOmFkc2sud2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) | 5.7 | 5.7 | 9.65

Nema17_25mm | 1 | Nema17_25mm v1 | Nema17_25mm v1 (https://gmail2024038.autodesk360.com/g/projects/20231224713178051/data/dXJuOmFkc2sud2lwcHJvZDpmcy5mb2xkZXI6Y28uMGxIVWluVGVSWTZtS2JGWFVKeEJkZw==/dXJuOmFkc2sud2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) | 42 | 46 | 47
DIN912_M3_6mm_SHCS | 25 | DIN912_M3_6mm_SHCS v1 | DIN912_M3_6mm_SHCS v1 (https://gmail2024038.autodesk360.com/g/projects/20231224713178051/data/dXJuOmFkc2sud2lwcHJvZDpmcy5mb2xkZXI6Y28uTktyRXlNMm5UcXFDbTlDbkJDRjZGQQ==/dXJuOmFkc2sud2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) | 5.5 | 5.5 | 9
4MM_E-Clip | 1 | 4MM_E-Clip v1 | 4MM_E-Clip v1 (https://gmail2024038.autodesk360.com/g/projects/20231224713178051/data/dXJuOmFkc2sud2lwcHJvZDpmcy5mb2xkZXI6Y28uMGxIVWluVGVSWTZtS2JGWFVKeEJkZw==/dXJuOmFkc2sud2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) | 0.7 | 7.739 | 8.85
3mm Rod Lock | 1 | 3mm Rod Lock | CNC_ToolChangeLock v1 (https://gmail2024038.autodesk360.com/g/projects/20231224713178051/data/dXJuOmFkc2sud2lwcHJvZDpmcy5mb2xkZXI6Y28uMGxIVWluVGVSWTZtS2JGWFVKeEJkZw==/dXJuOmFkc2sud2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) | 3 | 3 | 11
5mm Rod Lock | 1 | 5mm Rod Lock | CNC_ToolChangeLock v1 (https://gmail2024038.autodesk360.com/g/projects/20231224713178051/data/dXJuOmFkc2sud2lwcHJvZDpmcy5mb2xkZXI6Y28uMGxIVWluVGVSWTZtS2JGWFVKeEJkZw==/dXJuOmFkc2sud2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) | 5 | 5 | 56
T-Lock_Shim | 4 | T-Lock_Shim v1 | T-Lock_Shim v1 (https://gmail2024038.autodesk360.com/g/projects/20231224713178051/data/dXJuOmFkc2sud2lwcHJvZDpmcy5mb2xkZXI6Y28uMGxIVWluVGVSWTZtS2JGWFVKeEJkZw==/dXJuOmFkc2sud2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) | 0.38 | 6 | 6
94459A110_Heat-Set Inserts for Plastic | 12 | 94459A110_Heat-Set Inserts for Plastic | M2_3.4x2.5mm_Heat_Set_Insert v1 (https://gmail2024038.autodesk360.com/g/projects/20231224713178051/data/dXJuOmFkc2sud2lwcHJvZDpmcy5mb2xkZXI6Y28uTktyRXlNMm5UcXFDbTlDbkJDRjZGQQ==/dXJuOmFkc2sud2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) | 2.5 | 3.6 | 3.6
ISO7380_M3_45mm_BHHS | 1 | ISO7380_M3_45mm_BHHS v1 | ISO7380_M3_45mm_BHHS v1 (https://gmail2024038.autodesk360.com/g/projects/20231224713178051/data/dXJuOmFkc2sud2lwcHJvZDpmcy5mb2xkZXI6Y28uTktyRXlNMm5UcXFDbTlDbkJDRjZGQQ==/dXJuOmFkc2sud2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) | 5.7 | 5.7 | 46.65
DIN985_M3_Nylon_Lock_Washer | 5 | DIN985_M3_Nylon_Lock_Washer v1 | DIN985_M3_Nylon_Lock_Washer v1 (https://gmail2024038.autodesk360.com/g/projects/20231224713178051/data/dXJuOmFkc2sud2lwcHJvZDpmcy5mb2xkZXI6Y28uTktyRXlNMm5UcXFDbTlDbkJDRjZGQQ==/dXJuOmFkc2sud2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) | 4 | 5.5 | 6.351

DIN916_M3_4mm_Set_Screw | 8 | DIN916_M3_4mm_Set_Screw v1 | DIN916_M3_4mm_Set_Screw v1 (https://gmail2024038.autodesk360.com/g/projects/20231224713178051/data/dXJuOmFkc2sud2lwcHJvZDpmcy5mb2xkZXI6Y28uTktyRXlNMm5UcXFDbTlDbkJDRjZGQQ==/dXJuOmFkc2sud2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) | 2.927 | 2.927 | 4
CNC_Toolbank_Cooler_Passive_R2 | 1 | CNC_Toolbank_Cooler_Passive_R2 v1 | CNC_Toolbank_Cooler_Passive_R2 v1 (https://gmail2024038.autodesk360.com/g/projects/20231224713178051/data/dXJuOmFkc2sud2lwcHJvZDpmcy5mb2xkZXI6Y28uMGxIVWluVGVSWTZtS2JGWFVKeEJkZw==/dXJuOmFkc2sud2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) | 5 | 54.623 | 381.29
CNC_Silicone_Leak_Blocker | 5 | CNC_Silicone_Leak_Blocker v1 | CNC_Silicone_Leak_Blocker v1 (https://gmail2024038.autodesk360.com/g/projects/20231224713178051/data/dXJuOmFkc2sud2lwcHJvZDpmcy5mb2xkZXI6Y28uMGxIVWluVGVSWTZtS2JGWFVKeEJkZw==/dXJuOmFkc2sud2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) | 4.9 | 13.231 | 28.02
DIN7991_M3_10mm_FHHS | 10 | DIN7991_M3_10mm_FHHS v1 | DIN7991_M3_10mm_FHHS v1 (https://gmail2024038.autodesk360.com/g/projects/20231224713178051/data/dXJuOmFkc2sud2lwcHJvZDpmcy5mb2xkZXI6Y28uTktyRXlNMm5UcXFDbTlDbkJDRjZGQQ==/dXJuOmFkc2sud2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) | 6 | 6 | 10
DIN7991_M3_12mm_FHHS | 10 | DIN7991_M3_12mm_FHHS v1 | 6 | 6 | 12
CNC_Silicone_Wiper | 10 | CNC_Silicone_Wiper v1 | CNC_Silicone_Wiper v1 (https://gmail2024038.autodesk360.com/g/projects/20231224713178051/data/dXJuOmFkc2sud2lwcHJvZDpmcy5mb2xkZXI6Y28uMGxIVWluVGVSWTZtS2JGWFVKeEJkZw==/dXJuOmFkc2sud2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) | 1.5 | 14.567 | 32.341
DIN912_M3_16mm_SHCS | 13 | DIN912_M3_16mm_SHCS v1 | DIN912_M3_16mm_SHCS v1 (https://gmail2024038.autodesk360.com/g/projects/20231224713178051/data/dXJuOmFkc2sud2lwcHJvZDpmcy5mb2xkZXI6Y28uTktyRXlNMm5UcXFDbTlDbkJDRjZGQQ==/dXJuOmFkc2sud2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) | 5.5 | 5.5 | 19
Neodymium_Cylinder_Magnet_5x10mm | 5 | Neodymium_Cylinder_Magnet_5x10mm v1 | Neodymium_Cylinder_Magnet_5x10mm v1 (https://gmail2024038.autodesk360.com/g/projects/20231224713178051/data/dXJuOmFkc2sud2lwcHJvZDpmcy5mb2xkZXI6Y28uMGxIVWluVGVSWTZtS2JGWFVKeEJkZw==/dXJuOmFkc2sud2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) | 5 | 5 | 10
Linear_Shaft_4x30mm | 12 | Linear_Shaft_4x30mm v1 | Linear_Shaft_4x30mm v1 (https://gmail2024038.autodesk360.com/g/projects/20231224713178051/data/dXJuOmFkc2sud2lwcHJvZDpmcy5mb2xkZXI6Y28uMGxIVWluVGVSWTZtS2JGWFVKeEJkZw==/dXJuOmFkc2sud2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) | 4 | 4 | 30

DIN7991_M3_35mm_FHHS | 6 | DIN7991_M3_35mm_FHHS v1 | DIN7991_M3_35mm_FHHS v1 (https://gmail2024038.autodesk360.com/g/projects/20231224713178051/data/dXJuOmFkc2sud2lwcHJvZDpmcy5mb2xkZXI6Y28uTktyRXlNMm5UcXFDbTlDbkJDRjZGQQ==/dXJuOmFkc2sud2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) | 6 | 6 | 35
DIN7991_M3_8mm_FHHS | 8 | DIN7991_M3_8mm_FHHS v1 | DIN7991_M3_8mm_FHHS v1 (https://gmail2024038.autodesk360.com/g/projects/20231224713178051/data/dXJuOmFkc2sud2lwcHJvZDpmcy5mb2xkZXI6Y28uTktyRXlNMm5UcXFDbTlDbkJDRjZGQQ==/dXJuOmFkc2sud2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) | 6 | 6 | 8
toolboard PCB | 5 | toolboard PCB | PCB_ToolDock_CE v1 (https://gmail2024038.autodesk360.com/g/projects/20231224713178051/data/dXJuOmFkc2sud2lwcHJvZDpmcy5mb2xkZXI6Y28uMGxIVWluVGVSWTZtS2JGWFVKeEJkZw==/dXJuOmFkc2sud2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) | 1.6 | 13 | 50
PTFE_Bowden_Tube_5x3_74mm | 4 | PTFE_Bowden_Tube_5x3_74mm v1 | PTFE_Bowden_Tube_5x3_74mm v1 (https://gmail2024038.autodesk360.com/g/projects/20231224713178051/data/dXJuOmFkc2sud2lwcHJvZDpmcy5mb2xkZXI6Y28uMGxIVWluVGVSWTZtS2JGWFVKeEJkZw==/dXJuOmFkc2sud2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) | 5 | 5 | 74
DIN7991_M4_10mm_FHHS | 8 | DIN7991_M4_10mm_FHHS v1 | DIN7991_M4_10mm_FHHS v1 (https://gmail2024038.autodesk360.com/g/projects/20231224713178051/data/dXJuOmFkc2sud2lwcHJvZDpmcy5mb2xkZXI6Y28uTktyRXlNMm5UcXFDbTlDbkJDRjZGQQ==/dXJuOmFkc2sud2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) | 8 | 8 | 10
Linear_Shaft_4x15mm | 2 | Linear_Shaft_4x15mm v1 | Linear_Shaft_4x15mm v1 (https://gmail2024038.autodesk360.com/g/projects/20231224713178051/data/dXJuOmFkc2sud2lwcHJvZDpmcy5mb2xkZXI6Y28uMGxIVWluVGVSWTZtS2JGWFVKeEJkZw==/dXJuOmFkc2sud2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) | 4 | 4 | 15
Blower_Fan_30x30x10mm | 2 | Blower_Fan_30x30x10mm v1 | Blower_Fan_30x30x10mm v1 (https://gmail2024038.autodesk360.com/g/projects/20231224713178051/data/dXJuOmFkc2sud2lwcHJvZDpmcy5mb2xkZXI6Y28uMGxIVWluVGVSWTZtS2JGWFVKeEJkZw==/dXJuOmFkc2sud2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) | 10 | 30 | 30.041
ISO7380_M2_6mm_BHHS | 6 | ISO7380_M2_6mm_BHHS v1 | ISO7380_M2_6mm_BHHS v1 (https://gmail2024038.autodesk360.com/g/projects/20231224713178051/data/dXJuOmFkc2sud2lwcHJvZDpmcy5mb2xkZXI6Y28uTktyRXlNMm5UcXFDbTlDbkJDRjZGQQ==/dXJuOmFkc2sud2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) | 3.5 | 3.5 | 7.3
ISO7380_M2_8mm_BHHS | 2 | ISO7380_M2_8mm_BHHS | 3.5 | 3.5 | 9.3
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

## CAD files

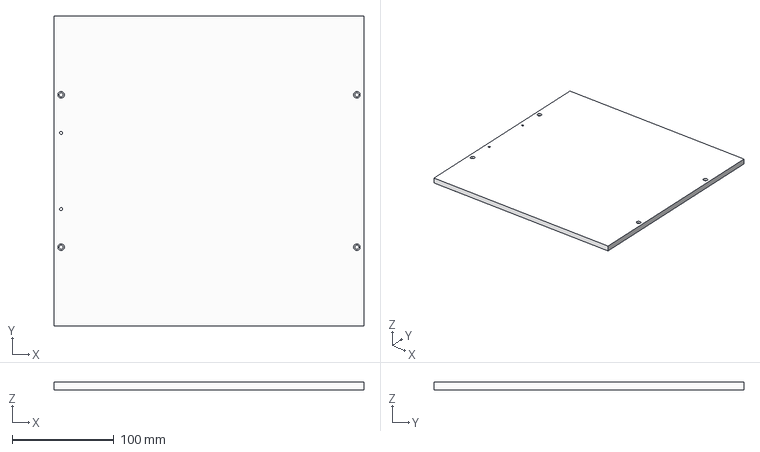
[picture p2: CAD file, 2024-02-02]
CAD/MIC6_Bed_V2_300.step
305.0 x 305.0 x 7.76 mm

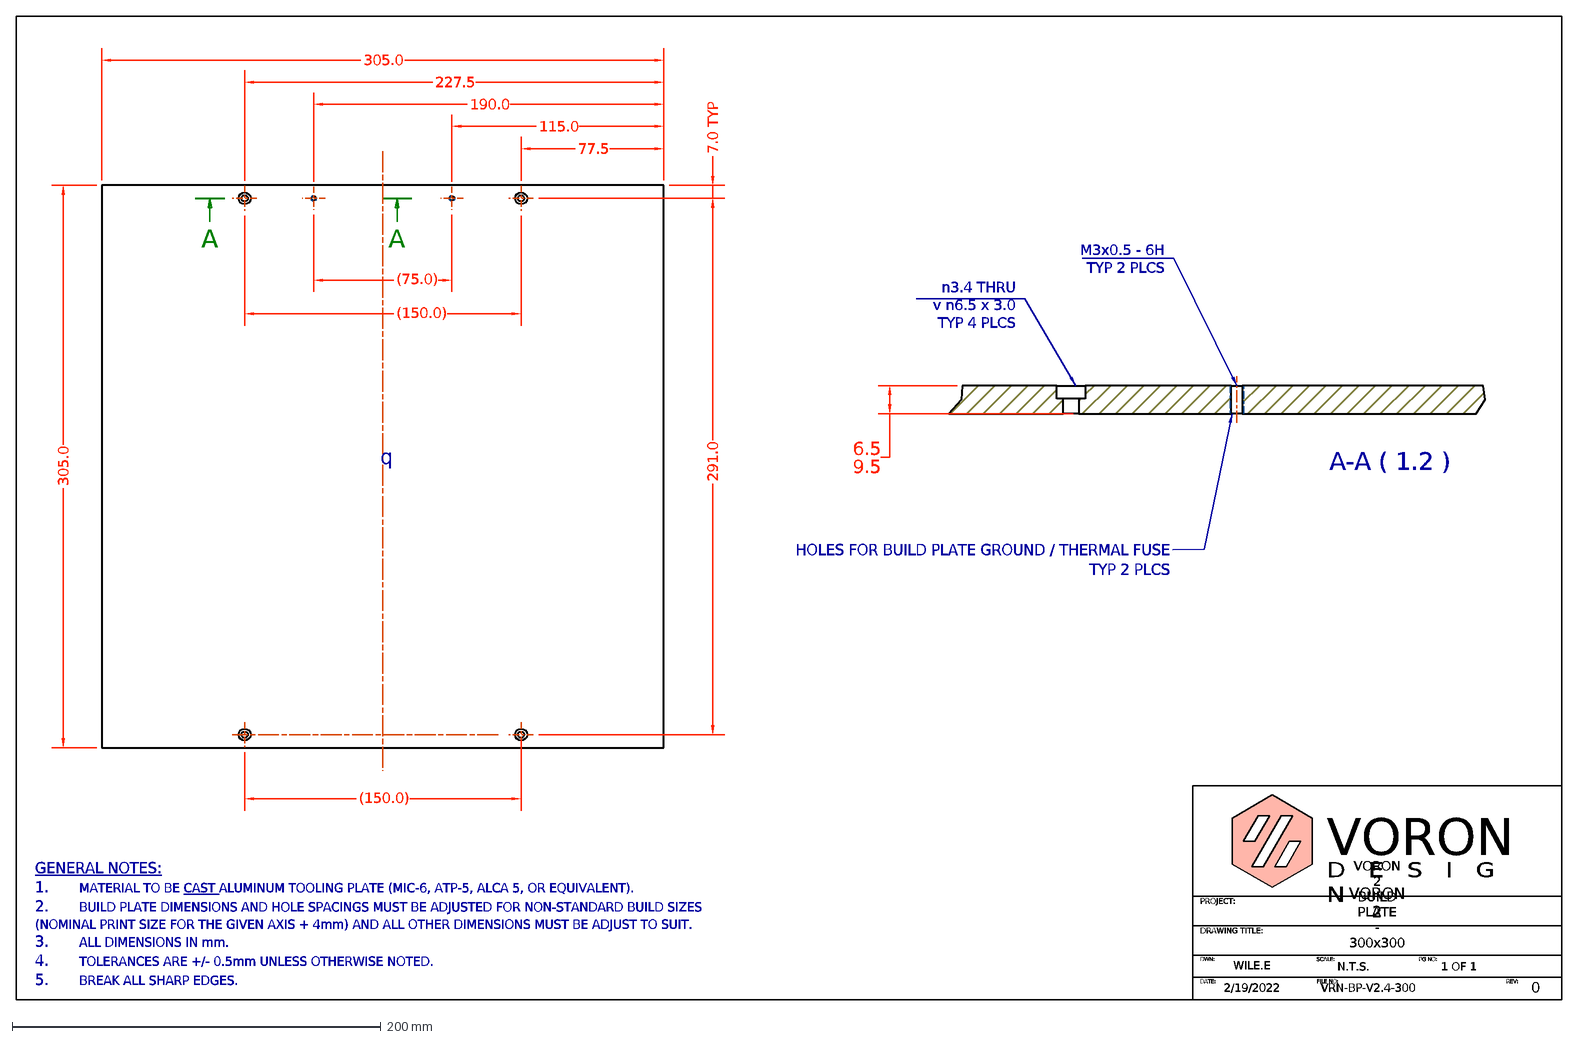
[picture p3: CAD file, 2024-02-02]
DXF/Build Plate/VORON_Design_-_2.4Build_Plate_300mm.dxf
2/19/2022
VRN-BP-V2.4-300
VORON 2
WILE.E
0
DATE:
FILE NO:
PROJECT:
DRAWING TITLE:
SCALE:
PG NO:
DWN:
1 OF 1
N.T.S.
VORON
D E S I G N
REV:
VORON 2 BUILD PLATE - 300x300
A
A-A ( 1.2 )
6.5^9.5
190.0
291.0
7.0 TYP
(150.0)
GENERAL NOTES: 1. MATERIAL TO BE CAST ALUMINUM TOOLING PLATE (MIC-6, ATP-5, ALCA 5, OR EQUIVALENT). 2. BUILD PLATE DIMENSIONS AND HOLE SPACINGS MUST BE ADJUSTED
305.0
115.0
227.5
HOLES FOR BUILD PLATE GROUND / THERMAL FUSE TYP 2 PLCS
77.5
M3x0.5 - 6H TYP 2 PLCS
(75.0)

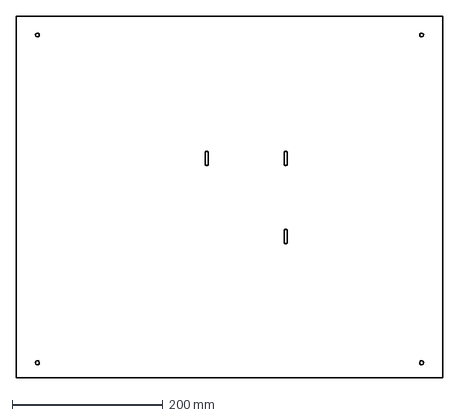
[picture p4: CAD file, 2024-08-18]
DXF/Enclosure/CNC_Acrylic_Panel_Rear.dxf
566.0 x 480.0 mm

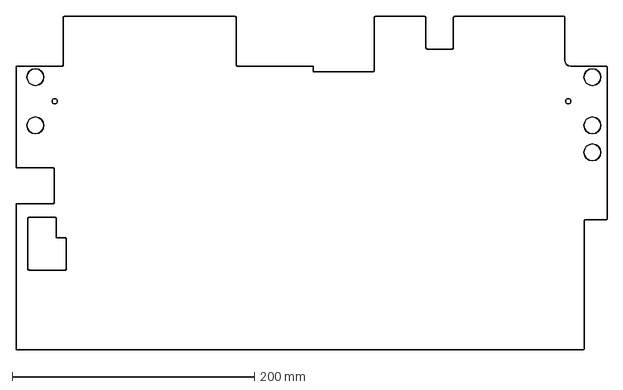
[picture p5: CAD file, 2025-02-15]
DXF/Enclosure/With PanelDue/CNC_Acrylic_Floor_Right_PanelDue7i.dxf
488.0 x 275.0 mm

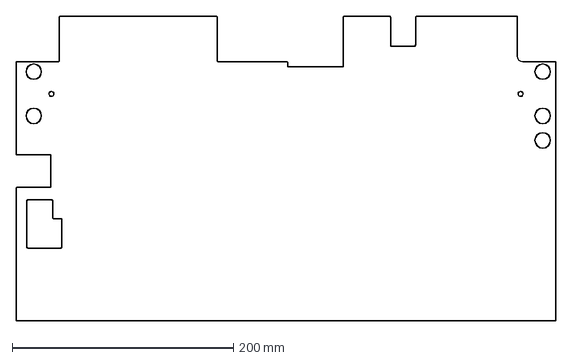
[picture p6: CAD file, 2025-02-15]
DXF/Enclosure/Without PanelDue/CNC_Acrylic_Floor_Right_Basic.dxf
488.0 x 275.0 mm

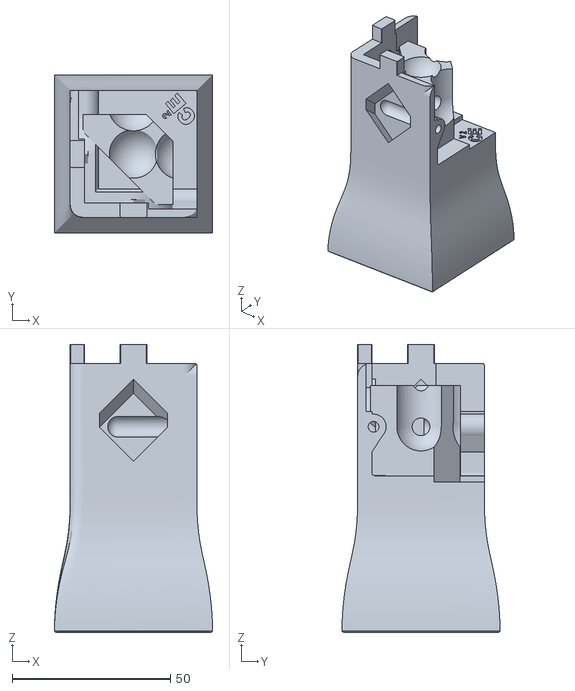
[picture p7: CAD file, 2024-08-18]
STLs/Guide 1 - Frame/Print_Corner_Bracket_Bottom_CE v4_QTY_4.stl
50.0 x 50.0 x 91.0

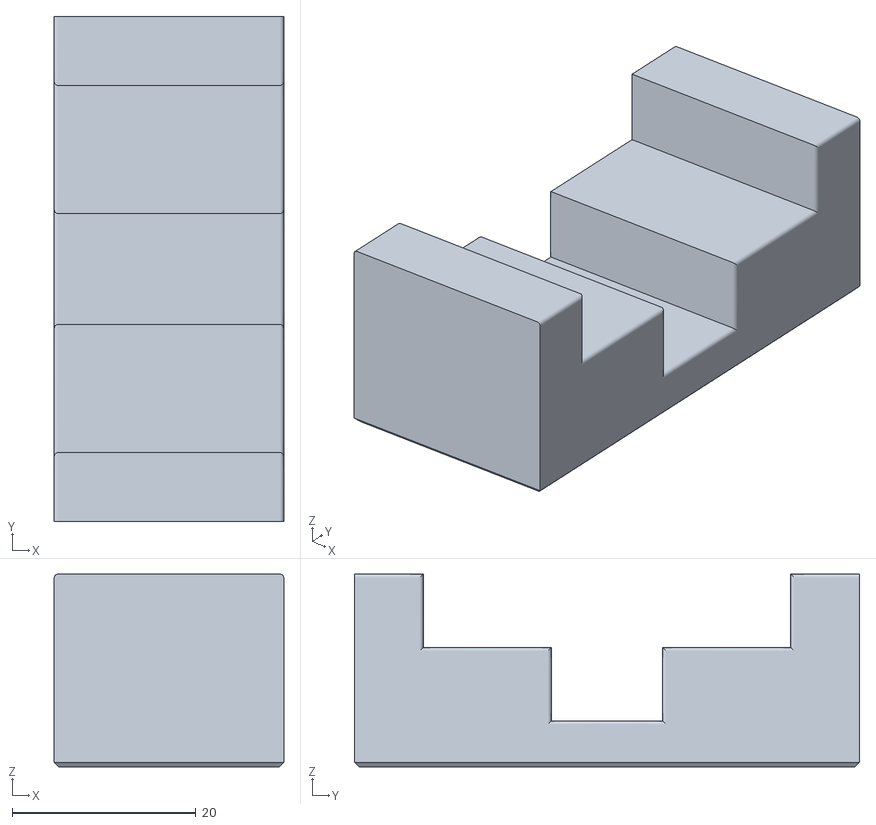
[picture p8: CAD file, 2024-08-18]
STLs/Guide 1 - Frame/Tools/Print_MGN12_Alignment_Block_4040 v2_QTY_12.stl
25.0 x 55.0 x 21.0

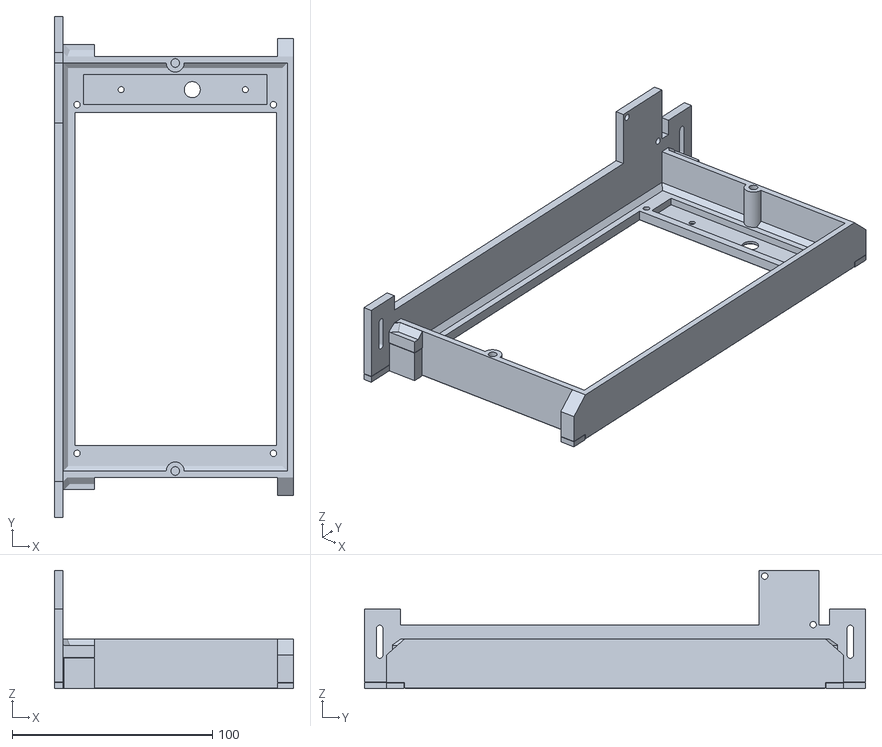
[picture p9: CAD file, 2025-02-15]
STLs/Guide 10 - Enclosure/Print_PanelDue7iMount v3_QTY_1.stl
119.4 x 250.0 x 59.1

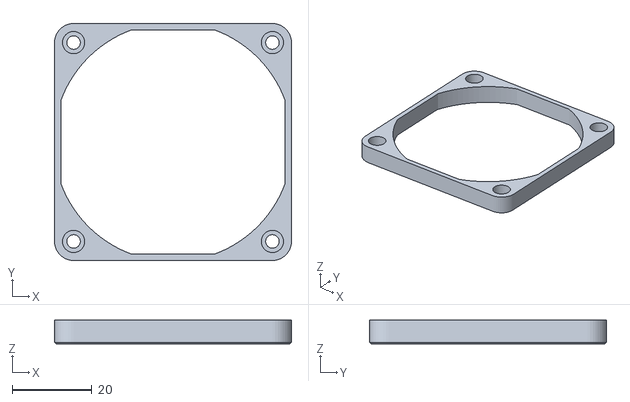
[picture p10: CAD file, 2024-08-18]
STLs/Guide 11 - Water Cooling/Print_FanShroud v3_QTY_1.stl
59.6 x 59.6 x 6.00

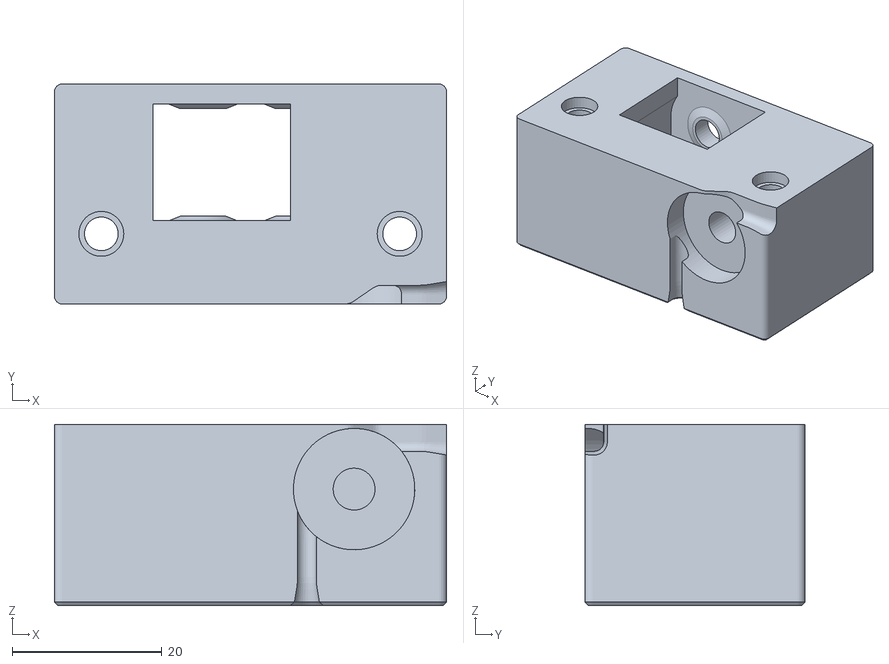
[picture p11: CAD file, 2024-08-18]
STLs/Guide 2 - Z Axis Motion/Print_Z-Axis_Belt_Idler_Left_Part_01 v2_QTY_1.stl
52.3 x 29.4 x 24.2

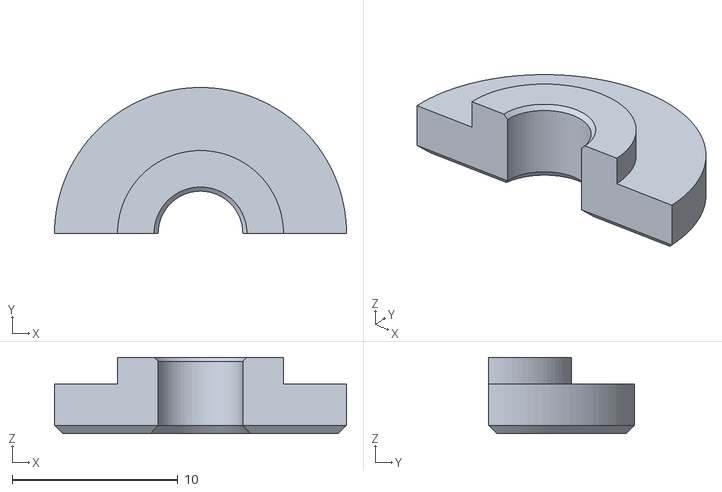
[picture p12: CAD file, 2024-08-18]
STLs/Guide 2 - Z Axis Motion/Tools/Print_Z-Axis_Motor_Installation_Tool_(4.6) v2_QTY_1.stl
17.6 x 8.80 x 4.60

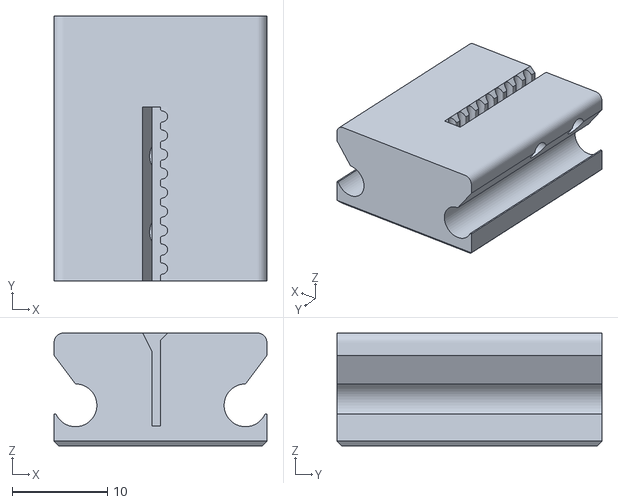
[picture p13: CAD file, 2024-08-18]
STLs/Guide 3 - Kinematic Bed/Print_Z-Axis_Belt_Tensioner_Right_Part_02_(1.52mm_Belt) v2_QTY_1.stl
22.4 x 27.9 x 11.9

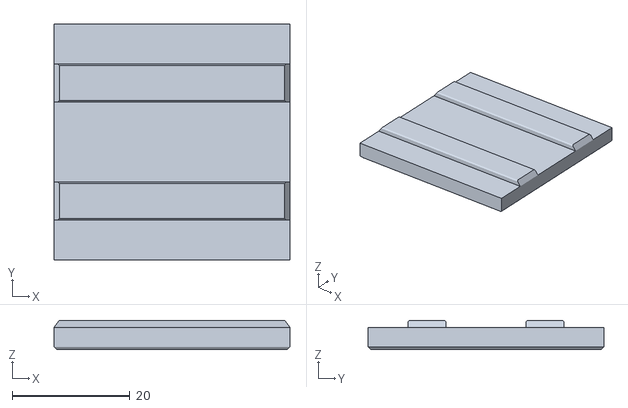
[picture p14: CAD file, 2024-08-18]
STLs/Guide 3 - Kinematic Bed/Tools/Print_Z-Axis_Left_Bed_Frame_Installation_Tool_(3.5)_CE v2_QTY_2.stl
40.0 x 40.0 x 5.00

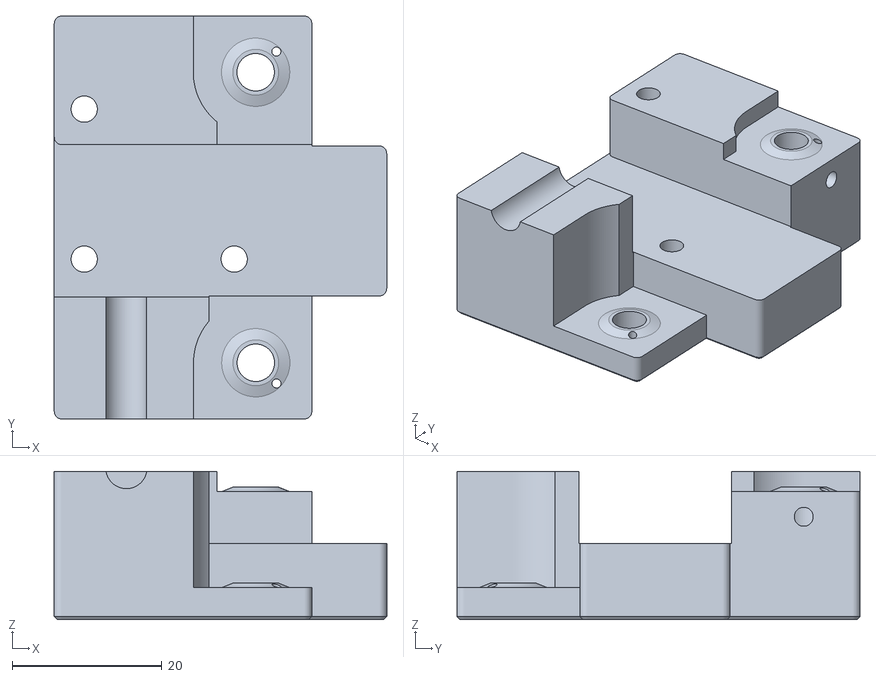
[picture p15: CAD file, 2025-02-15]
STLs/Guide 4 - XY Motion/Print_Y-Axis_Bracket_Rear_Bottom_(1.52mm) v2_QTY_1.stl
44.3 x 53.7 x 19.8

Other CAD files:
STLs/Guide 4 - XY Motion/Tools/Print_X-Axis_Linear_Rail_Installation_Tool_(56.50)_CE v2_QTY_1.stl
STLs/Guide 5 - Standard Tool Lock/Print_ToolLockIndex_V2 v4_QTY_1.stl
STLs/Guide 5 - Standard Tool Lock/Tools/Print_Standard_Lock_Motor_Installation_Tool_(1.7) v1_QTY_1.stl
STLs/Guide 6 - Tooldock/Print_ToolDockSpacer_Part_02 v2_QTY_5.stl
DXF/Enclosure/Acrylic_Front_Door.dxf
DXF/Enclosure/CNC_Acrylic_Panel_Left.dxf
DXF/Enclosure/CNC_Acrylic_Panel_Right.dxf
DXF/Enclosure/With PanelDue/CNC_Acrylic_Floor_Left_PanelDue7i.dxf
DXF/Enclosure/With PanelDue/CNC_Acrylic_Front_PanelDue7i.dxf
DXF/Enclosure/Without PanelDue/CNC_Acrylic_Floor_Left_Basic.dxf
DXF/Enclosure/Without PanelDue/CNC_Acrylic_Front_Basic.dxf
STLs/Guide 1 - Frame/Print_Corner_Bracket_Bottom_Lock_CE v2_QTY_4.stl
STLs/Guide 1 - Frame/Print_Corner_Bracket_Lock_CE v2_QTY_12.stl
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

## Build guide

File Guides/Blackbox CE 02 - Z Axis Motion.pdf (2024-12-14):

### Z Axis Motion

# BLACKBOX CE

DOCUMENTATION VERSION 1

Version | Notes

## 1 Initial Release

# Change Log

# Blackbox CE Mechanical Assembly: 02. Z Axis Motion

### Authored by Daniel Darms

## Description M3x0.5mm Tap Electric Drill Hand Tap Wrench Hex Wrenches Reamers Threadlocker Soldering Iron with Heatset insert tip

# Tools

# Parts

QTY | Description | Material | Ver | Link
2 | Print_Z-Axis_40t_Pulley_Installation_Tool_(7.551) | PLA | 1
1 | Print_Z-Axis_80t_Pulley_Installation_Tool_(122.5) | PLA | 1
1 | Print_Z-Axis_EF10_Installation_Tool_(160.006)_CE | PLA | 1
1 | Print_Z-Axis_EK8_Installation_Tool_(169.006)_CE | PLA | 1
1 | Print_Z-Axis_Idler_Pulley_Installation_Tool_(168.889)_CE | PLA | 1
1 | Print_Z-Axis_Motor_Installation_Tool_(4.6) | PLA | 1
1 | Print_Pulley_Reduction_40t_Pulley_Installation_Tool_(1.85) | PLA | 1
1 | Print_Pulley_Reduction_16t_Pulley_Installation_Tool_(0.9) | PLA | 1
1 | Print_PulleyReduction_part02 | >=ABS | 1
2 | Print_PulleyReduction_part03 | >=ABS | 1
1 | Print_PulleyReduction_part01_CE | >=ABS | 1
1 | Print_Z-Axis_Motor_Bracket | >=ABS | 1
1 | Print_2020_Corner_Bracket_Lock_Part_01_CE | >=ABS | 1
2 | Print_2020_Corner_Bracket_Lock_Part_02_CE | >=ABS | 1
1 | Print_EK8_Spacer | >=ABS | 1
2 | Print_EF10_Liner | >=ABS | 1
2 | Print_EK8_Liner | >=ABS | 1
1 | Print_Z-Axis_Belt_Idler_Right_Part_01 | >=ABS | 1
1 | Print_Z-Axis_Belt_Idler_Right_Part_02_CE | >=ABS | 1
2 | Print_Z-Axis_Tackle_Roller | >=ABS | 1
1 | Print_Z-Axis_Belt_Idler_Left_Part_01 | >=ABS | 1
1 | Print_Z-Axis_Belt_Idler_Left_Part_02_CE | >=ABS | 1

# Printed Parts

## Step 1 – Preparation

For this secon a small hand vise or small arbor press is listed in tools. This will be used for pressing linear shas through bearings if needed. Never bang on bearings to install them. The impact to the outer race of a small bearing will cause flat spots on the actual bearing balls. These flat spots will cause
fricon and heat that both reduces the life of the bearing and introduces drag resistance. Dropping a bearing will have the same result. If you drop a bearing onto a hard surface, it is best to discard and replace it. If you find a linear sha to have excessive resistance during installaon, the first thing to try is to insert the linear sha from the other end. If both ends of the linear sha seem to have excessive resistance, then you can install the linear sha into your hand drill. Pinch a small piece of fine grit sandpaper (#4000) onto one end as you operate the drill for a few seconds. For the printed parts, all the Installaon Tools may be printed in a cheaper material such as PLA. For the through holes of printed parts, verify that a reamer of the same size will fit through. If there is resistance in the hole, use the reamer unl the hole is free and clear. Both M3 and M4 heat set inserts are used in this guide. Most soldering iron installaon kits for heat set inserts have a different p for M3 and M4 inserts. You will need to let the iron cool aer installing inserts of one size before switching to the other installaon p to connue with the other size.

## Step 2 – Pulley Reduction Housing

Locate the printed Pulley Reducon Part 02 and insert two M4 heat set inserts into the top of the printed part.

Insert two M3 heat set inserts into the le side, then rotate the part 180 degrees and repeat with two M3 heat set inserts on the right side.

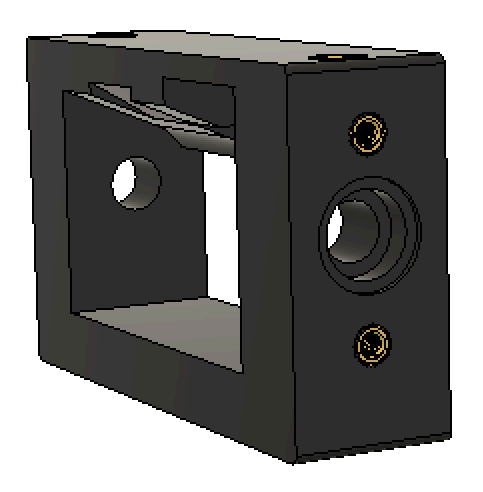
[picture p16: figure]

Insert a flanged 5x10x4 bearing into the pocket on the le face of the printed part.

Locate the GT2 77tooth loop belt 9x154 and place it around the GT2 40t pulley with 5mm bore.

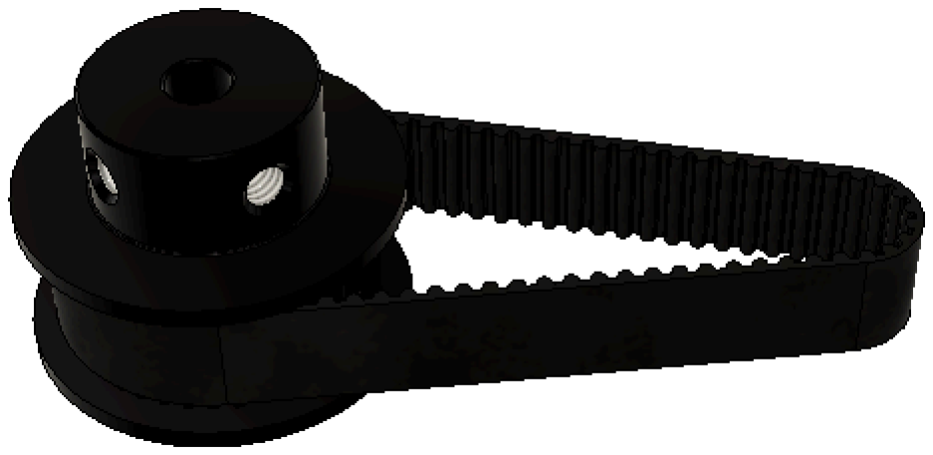
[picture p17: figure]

Place the GT2 40t pulley into the printed part with the hub facing toward the right (le for perspecve of picture) of the printed part. The pulley can only fit into the part one way. Press the 5x70mm linear sha through the flanged bearing, through the printed part, and through the GT2 40t pulley unl it just protrudes from the hub of the pulley.

Locate the GT2 94tooth 9x188 loop belt and place it around a GT2 16t pulley with 5mm bore.

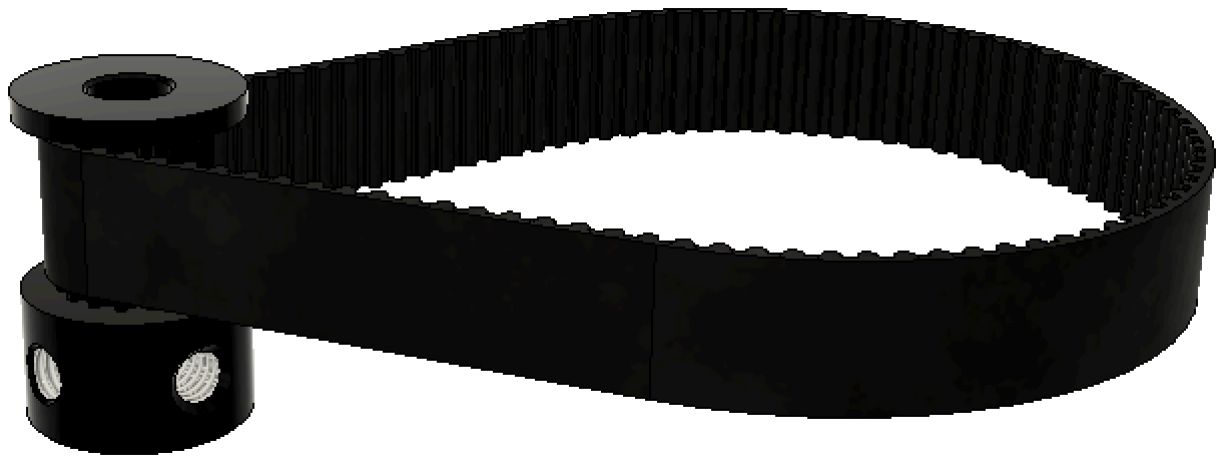
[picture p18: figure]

Insert a flanged 5x10x4 bearing into the pocket on the right face of the printed part. Insert the GT2 16t pulley into the printed part with the hub facing the hub of the 40t pulley. Connue to press the 5x70mm linear sha through the 16t pulley, through the printed part, and through the 5x10x4 flanged bearing. Squeeze each end of the 5x70mm linear sha to center it into the printed part.

Locate the two printed Pulley Reducon Part 03. You will noce that one face of these printed parts has a recess. Install one of these printed parts onto the right of the Pulley Reducon assembly with the recess facing the flanged 5x10x4 bearing, then secure with two M3x8mm SHCS. Repeat this with the other printed part and two more M3x8mm SHCS on the le end of the Pulley Reducon Assembly.

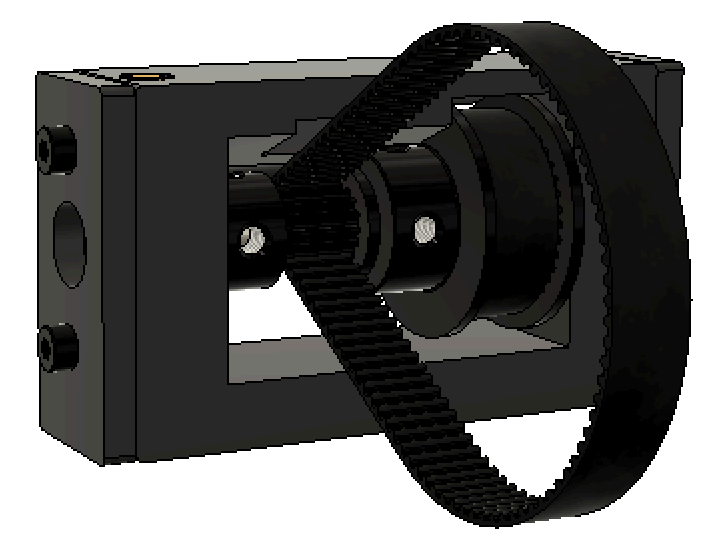
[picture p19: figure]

Rotate the assembly and insert the printed Pulley Reducon 40t Installaon Tool between the flat face of the 40t pulley and the printed Pulley Reducon Part 02.

From the rear side of the Pulley Reducon assembly, secure the 40t pulley to the 5x70mm sha. Apply medium strength thread locker to two M4x6mm Set Screws. Hold the 40t pulley ght to the le of the Pulley Reducon Assembly using the printed tool to set the proper clearance. Tighten the M4x6mm set screws into the hub of the 40t pulley completely. You may need to rotate the 40t pulley to access one or both of the set screw holes in the hub.

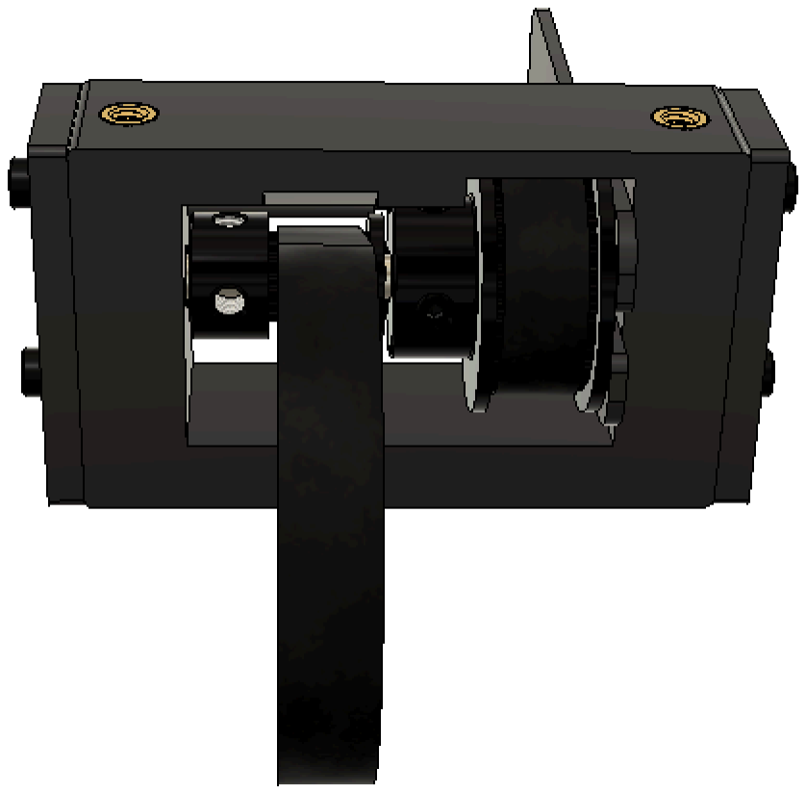
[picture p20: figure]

Rotate the assembly and insert the printed Pulley Reducon 16t Installaon Tool between the hub of the 40t pulley and the hub of the 16t pulley.

From the rear side of the Pulley Reducon assembly, secure the 16t pulley to the 5x70mm sha. Apply medium strength thread locker to two M4x4mm Set Screws. Hold the 16t pulley ght to the le of the Pulley Reducon Assembly using the printed tool to set the proper clearance. Tighten the M4x4mm set screws into the hub of the 16t pulley completely. You may need to rotate the 16t pulley to access one or both of the set screw holes in the hub.

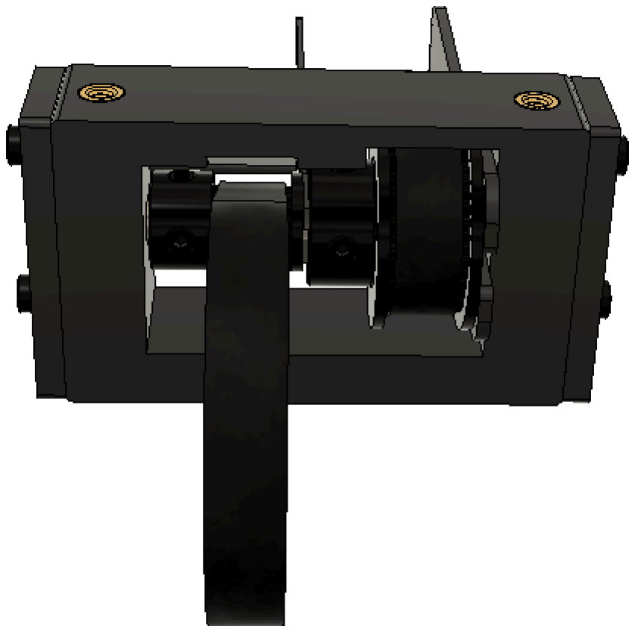
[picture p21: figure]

Remove the printed Pulley Reducon Installaon Tools. Place the printed Pulley Reducon Part 01 on top of the Pulley Reducon Assembly and secure with two M4x20 SHCS.

## Step 3 – Z-Axis Motor

Set the Pulley Reducon Assembly aside and locate a NEMA17 motor. Place the printed Z-Axis Motor Installaon Tool onto the sha of the NEMA17 motor.

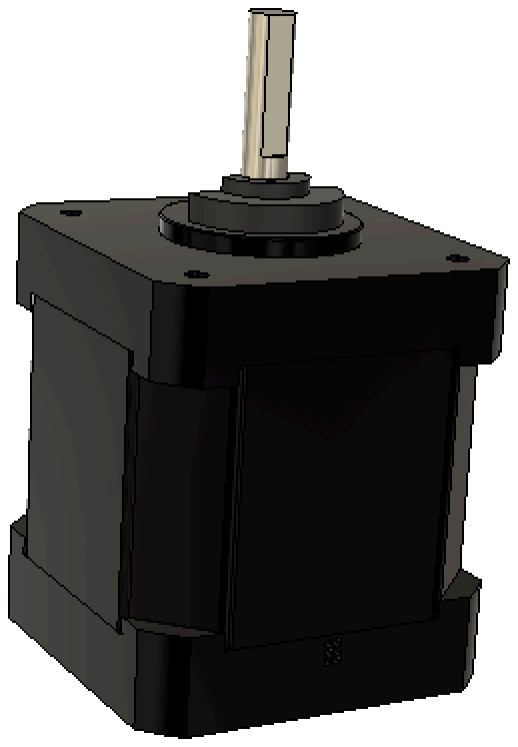
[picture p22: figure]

Install a GT2 16t pulley with 5mm bore onto the NEMA17 motor sha. Align one of the set screw holes with the flat of the motor sha. Coat two M4x4mm set screws with medium strength thread locker. Secure the 16t pulley to the NEMA17 motor sha with the two M4x4mm set screws securely. Start by securing the set screw facing the flat of the motor sha. As this screw ghtens, wiggle the 16t pulley to assure the flat end of the set screw mates flush with the flat of the NEMA17 motor sha. Keep the hub of the 16t pulley ght with the printed Installaon Tool to set the proper pulley height. Tighten both M4x4mm set screws completely.

Remove printed Installaon Tool. Orient motor as below with connecon for wiring harness facing you. Place the printed Z-Axis Motor Bracket onto the NEMA17 motor and secure it with four M3x10mm SHCS.

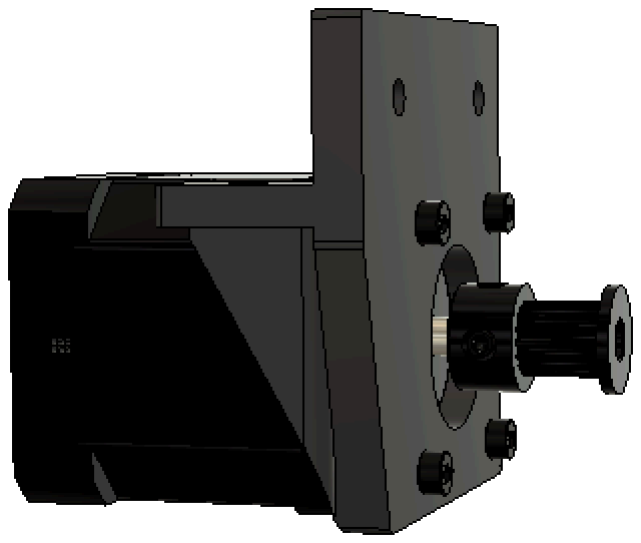
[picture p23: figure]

## Step 4 – Z-Axis Drive Shaft

Set the Z-Axis Motor Assembly aside. Turn your assembled frame upside down and orient the front toward you. Insert two M4 Slot 6 roll-in nuts into the center slot of the le (right as to perspecve of picture) 2060 extrusion as shown.

Place the EF10 Bearing on top of the le 2060 extrusion. Line up the holes in the M4 Slot 6 roll-in nuts with the mounng holes in the EF10 Bearing.

Place a printed EF10 liner into each of the mounng holes of the EF10 Bearing. Insert an M4x35mm SHCS through an M4 Fender Washer, then through the printed EF10 Liner, and into the M4 Slot 6 roll-in nut. Loosely ghten the M4x35mm SHCS and repeat for the other EF10 Bearing mounng hole with another M4x35 SHCS and M4 Fender Washer.

Place the ribs of the printed Z-Axis EF10 Installaon Tool into the center slot of the 2060 rail between the EF10 Bearing and the front 470mm 4040 extrusion. Slide the EF10 Bearing assembly unl it is flush with the printed installaon tool and the printed installaon tool is flush to the 470mm 4040 extrusion. Fully ghten all the M4x35 SHCS.

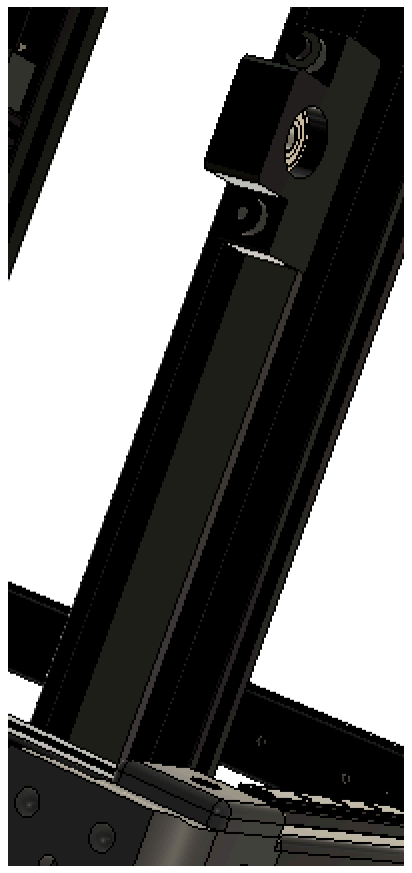
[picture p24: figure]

Remove the printed EF10 Installaon Tool. Locate the printed Z-Axis 80t Pulley Installaon tool. Slide the 8x520mm linear sha into the printed tool unl it is flush to the boom. Install the GT2 80t pulley so the flat side of the pulley is flush with the printed tool. Coat two M5x12mm set screws with medium strength thread locker. Secure the 80t pulley to the 8x520mm linear rod with the two M5x12mm set screws. Tighten the two M5x12mm set screws completely.

Remove the printed tool from the linear sha. If you find it difficult to remove the printed tool, you can install a M3 heat set insert into the boom of the printed tool while it is sll aached to the linear sha,

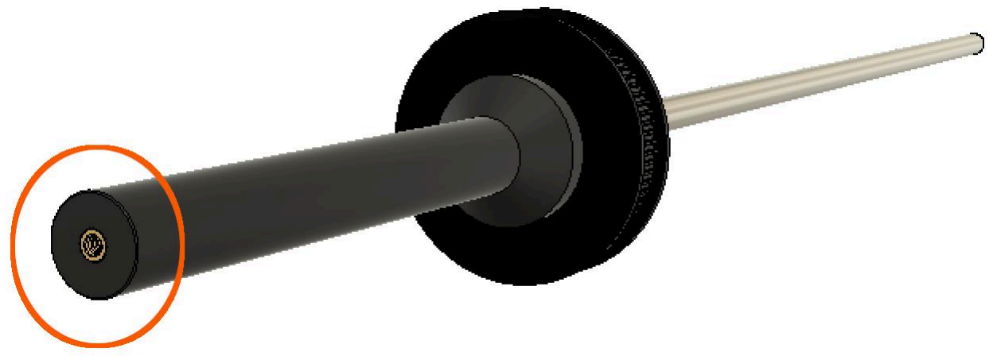
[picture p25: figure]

Then use a long M3 SHCS to press the linear sha far enough away from the printed tool to facilitate easy removal.

Place two M4 Slot 6 roll-in nuts into the center slot of the right (le in perspecve to picture) 2060 extrusion as shown.

Place the printed part EK8 Spacer on top of the 2060 extrusion and align the holes of the M4 Slot 6 roll-in nuts with the holes in the printed part.

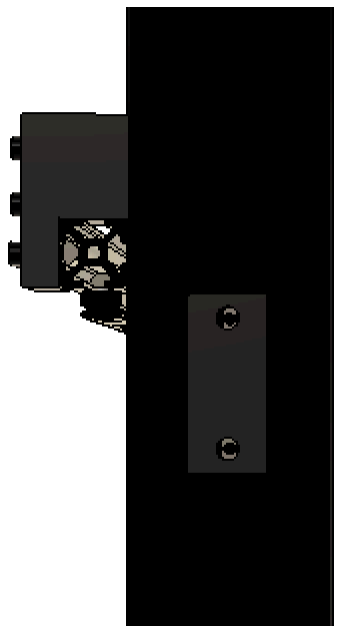
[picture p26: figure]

Wrap the GT2 94t 9x188mm loop belt from the Pulley Reducon assembly around the GT2 80t pulley mounted on the 8x520mm linear sha. It is okay if the Pulley Reducon Assembly is dangling at this point. Slide the EK8 Bearing onto the 8x520mm linear sha at the end opposite the 80t pulley. If a bearing guide is present on one side of the EK8 bearing, orient that side toward the 80t pulley. Place the EK8 Bearing with 520mm linear rod assembly installed on top of the printed EK8 spacer. Be certain the EK8 Bearing is oriented properly over the printed EK8 Spacer. Locate the printed EK8 Liner parts and install one into each mounng hole of the EK8 bearing. Insert an M4x45mm SHCS through an M4 Fender Washer, through the printed EK8 Liner, and into the M4 Slot 6 roll-in nut. Repeat for the other EK8 Bearing mounng hole with another M4x45mm SHCS and M4 Fender Washer. Loosely secure both M4x45 SHCS. Slide the opposite end of the 8x520mm linear sha (end closer to 80t pulley) through the secured EF10 Bearing. You may need to slide the EK8 Bearing assembly from front to back (up or down in perspecve of picture) to line up 520mm linear sha with the secured EF10 Bearing.

Place the ribs of the printed Z-Axis EK8 Installaon Tool into the center slot of the 2060 rail between the EK8 Bearing and the front 470mm 4040 extrusion. Slide the EK8 Bearing assembly unl it is flush with the printed installaon tool and the printed installaon tool is flush to the 470mm 4040 extrusion. Fully ghten all the M4x45 SHCS.

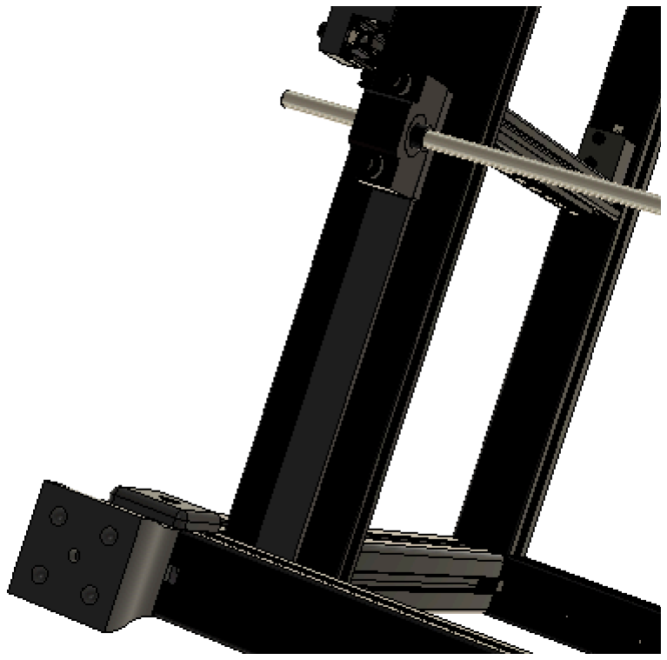
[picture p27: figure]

Remove the printed EF10 Installaon Tool.

## Step 5 – Pulley Reduction Assembly Brace

Place a 1020 extrusion of 350mm in front of you with the slot facing up. Install three M4 Slot 6 roll-in nuts as shown.

Place Print_2020_Corner_Bracket_Lock_Part_01_CE on the outside of a 2020 Corner Bracket as shown.

Now insert a Print_2020_Corner_Bracket_Lock_Part_02_CE through one of the holes of the 2020 Corner Bracket unl it is flush with the bracket and locked into the printed Part 01.

Repeat for the other hole of the 2020 Corner Bracket with another printed Part 02.

Place the assembled 2020 Corner Bracket on the extrusion at the right end. Align the bracket flush and secure with an M4x8mm BHHS through an M4 washer. Tighten the M4x8mm BHHS securely.

Move the Pulley Reducon Assembly out of the way and place an M4 Slot 6 roll-in nut into the side slot of the le 2060 extrusion as shown.

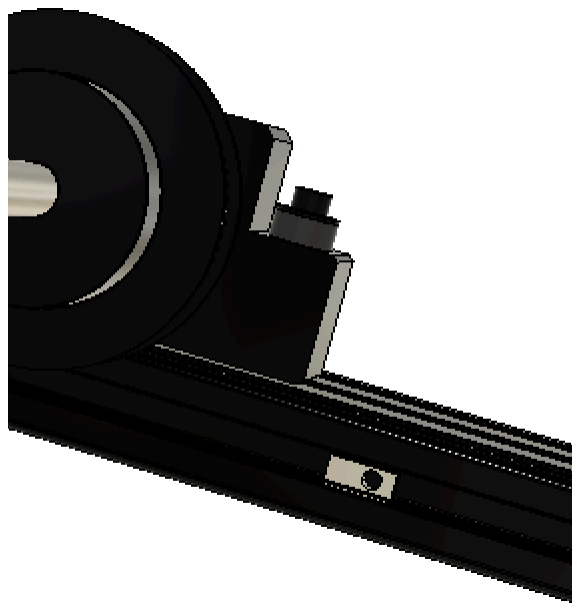
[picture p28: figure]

Move the Pulley Reducon Assembly back into posion and insert an M4x14mm SHCS through the Pulley Reducon Assembly into the M4 Slot 6 roll-in nut. Loosely fasten the M4x14mm SHCS.

Hold the assembled 1020 extrusion against the Pulley Reducon Assembly and move the M4 Slot 6 roll-in nuts unl they line up with the holes in the Pulley Reducon Assembly.

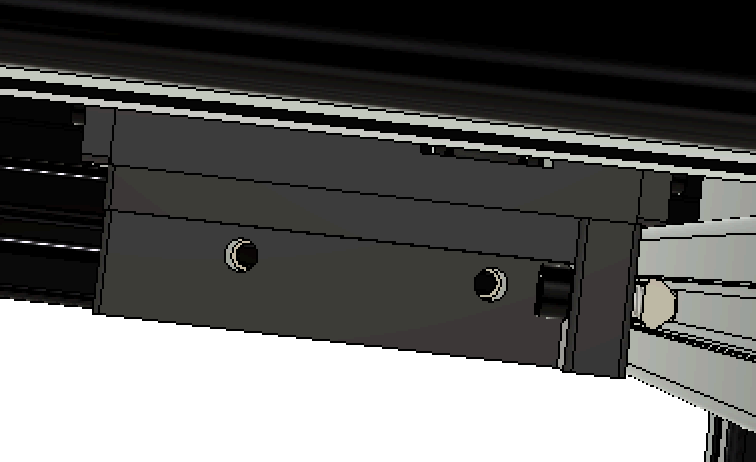
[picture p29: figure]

Put the assembled 1020 extrusion down. Install an M4 Slot 6 roll-in nut on the side of the right 2060 extrusion as shown.

Place the assembled 1020 extrusion against the Pulley Reducon Assembly again. Secure the Pulley Reducon Assembly to the 1020 extrusion with two M4x22mm SHCS. Keep the 1020 extrusion flush to the le 2060 extrusion and ghten the two M4x22mm SHCS completely.

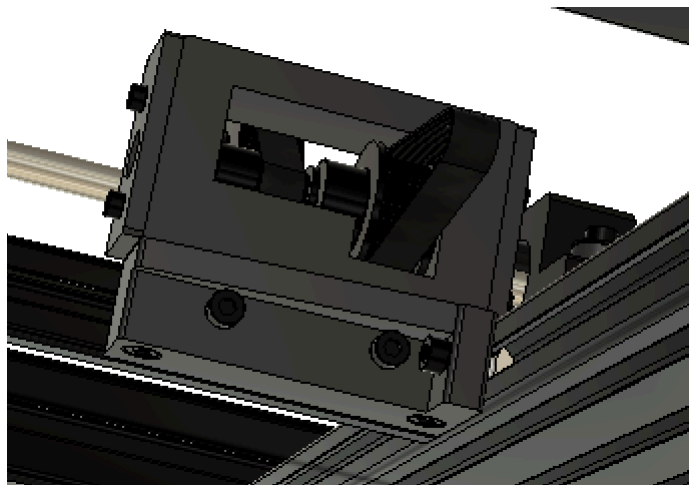
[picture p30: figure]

At the other end of the 1020 extrusion, secure the 2020 Corner Bracket to the right 2060 extrusion by inserng an M4x8mm BHHS through an M4 washer, through the 2020 Corner Bracket, and into the M4 Slot 6 roll-in nut. Loosely secure the M4x8mm BHHS.

Moving the 1020 extrusion of the Pulley Reducon Assembly away from the 8x520mm linear sha will set the tension for the GT2 94t 9x188mm Loop Belt. Move this assembly now and set the belt tension. Be certain to measure each end of the 1020 extrusion to the end of its corresponding 2060 extrusion to keep the 1020 extrusion perpendicular. When the GT2 94t 9x188mm Loop Belt is properly tensioned and the measurements of the 1020 extrusion are equal to a reference frame part, ghten the M4x8mm BHHS completely at the 2020 Corner Bracket.

And ghten completely the M4x14mm SHCS of the Pulley Reducon Assembly.

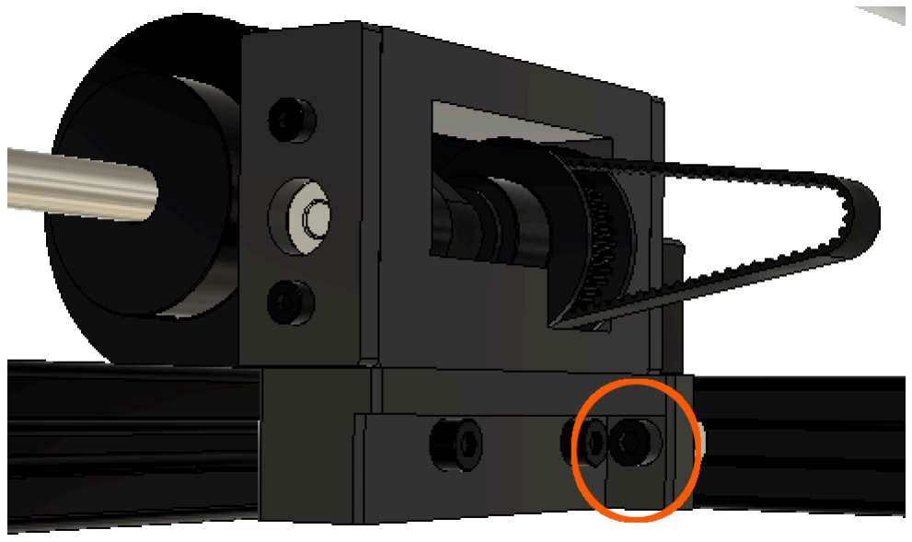
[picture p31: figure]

## Step 6 – Z-Axis Motor Tensioner

Place two M4 Slot 6 roll-in nuts into the side of the le 2060 extrusion as shown.

Place an M4 Slot 6 roll-in nut into the boom of the le 2060 extrusion as shown.

Guide the GT2 16t pulley of the Z-Axis Motor assembly into the GT2 75t 9x154mm Loop Belt of the Pulley Reducon Assembly. Orient the Z-Axis Motor assembly as shown and secure to the 2060 extrusion with one M4x10mm SHCS into the M4 Slot 6 roll-in nut on the boom of the 2060 extrusion and two M4x12mm SHCS into the M4 Slot 6 roll-in nuts on the side of the 2060 extrusion. Loosely secure these screws. Slide the Z-Axis Motor assembly away from the Pulley Reducon assembly to set the proper tension of the GT2 77t 9x154mm Loop Belt. With the proper tension of the loop belt achieved, completely secure all the SHCS aaching the Z-Axis Motor Assembly to the 2060 extrusion.

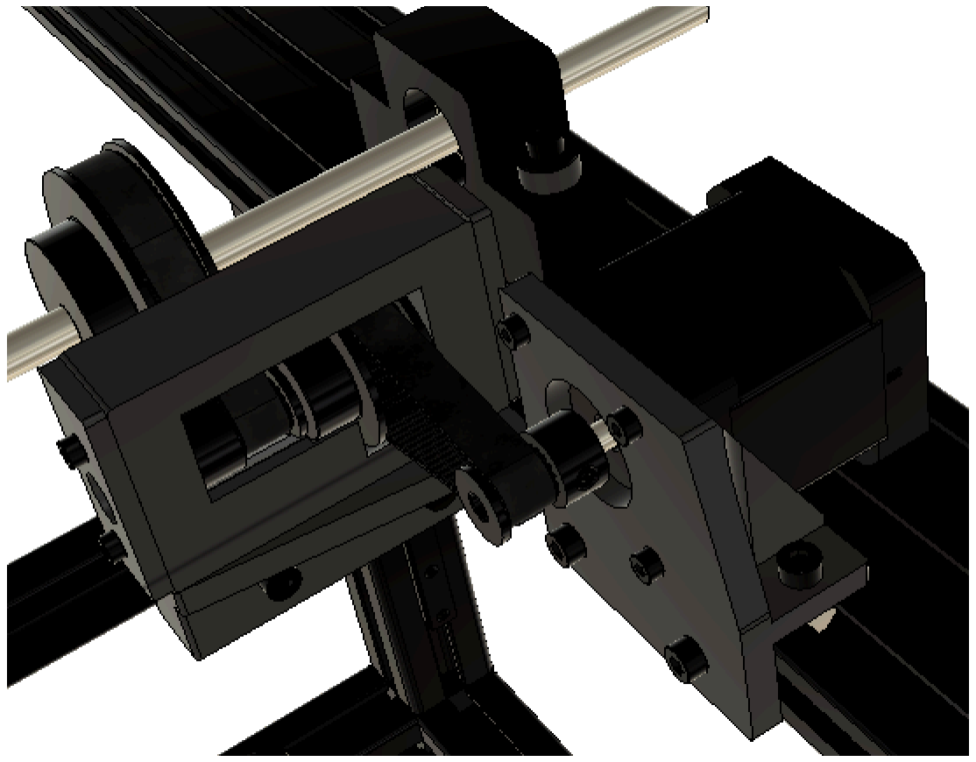
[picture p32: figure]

## Step 7 – Z-Axis Belt Pulleys

Locate a GT2 40t Pulley with 8mm Bore. Slide the 40t pulley onto the le end of the 8x520mm linear sha with hub facing inward. Now slide the printed Z-Axis 40t Pulley Installaon Tool onto the end of the 8x520mm linear sha. Coat two M4x4 set screws with medium strength thread locking compound. Hold the 40t pulley against the Installaon tool and secure it to the 8x520mm linear sha with the two M4x4mm set screws. Fully ghten both M4x4mm set screws. You may need to rotate the 8x520mm sha to access the holes for one or both set screws.

Remove the printed Installaon Tool. Repeat the above steps to install the other GT2 40t Pulley with 8mm Bore on the right end of the 8x520mm linear sha using the printed Installaon Tool and two M4x4mm set screws coated in medium strength thread locker.

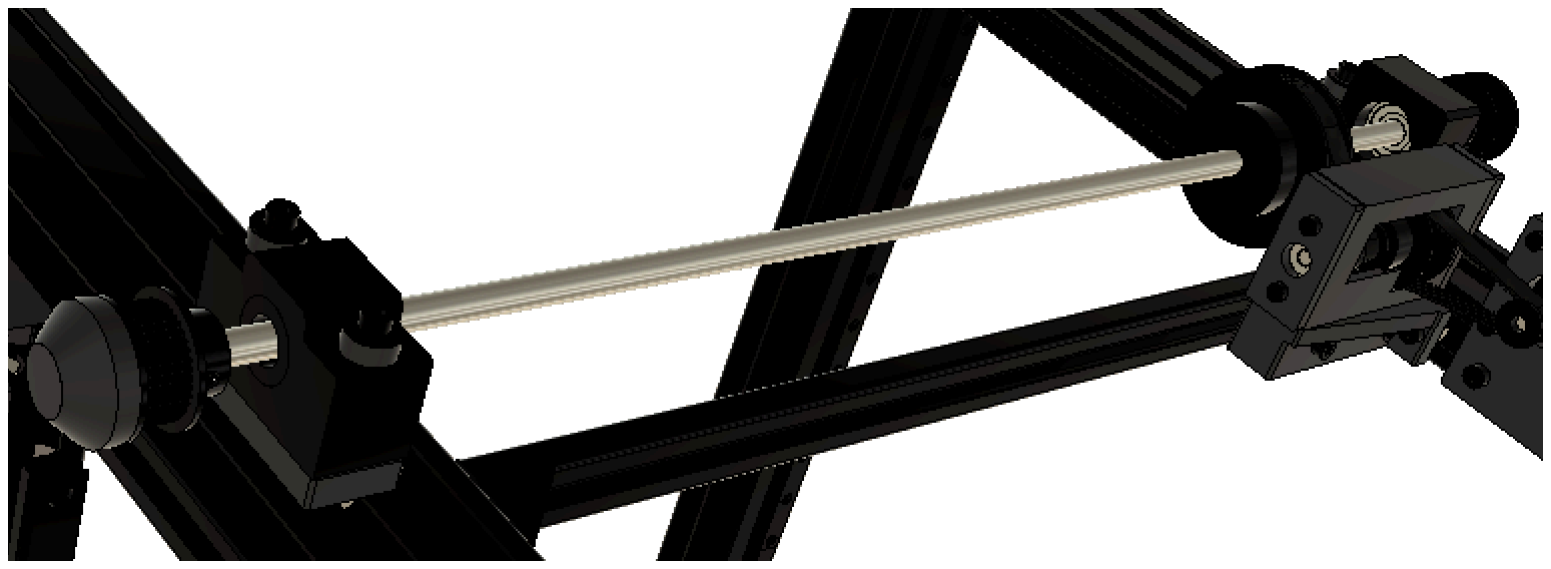
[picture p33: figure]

## Step 8 – Z-Axis Idler Pulleys

The Z-Axis Idlers are mirrored parts of each other. We will build the right side idler with diagrams and then you will build the le side to mirror this one. Start with printed Z-Axis Belt Idler Right Part 01 and tap M3 threads into the plasc at the locaons shown. Tap the holes unl they intersect with the 5mm hole coming from the back of the part.

Place an M4 heat set insert into the hole as shown.

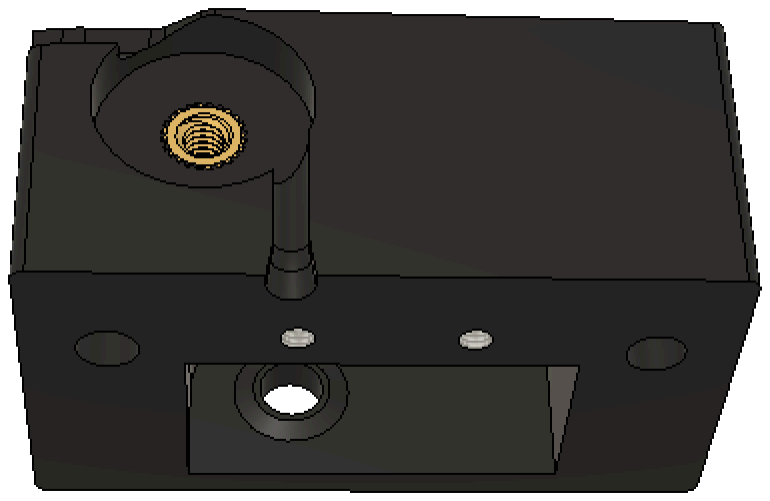
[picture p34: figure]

Orient the part as shown and snap a GT2 20t Idler Pulley with 5mm Bore into printed part. The upper Idler Pulley must be installed first.

Press a 5x25mm Linear Sha through the hole in the top of the printed part and fully through the Idler Pulley unl the end of the linear sha is flush with the rear (top in perspecve of picture) of the printed part. Use the hand vise or arbor press if the linear sha seems difficult to press in by hand.

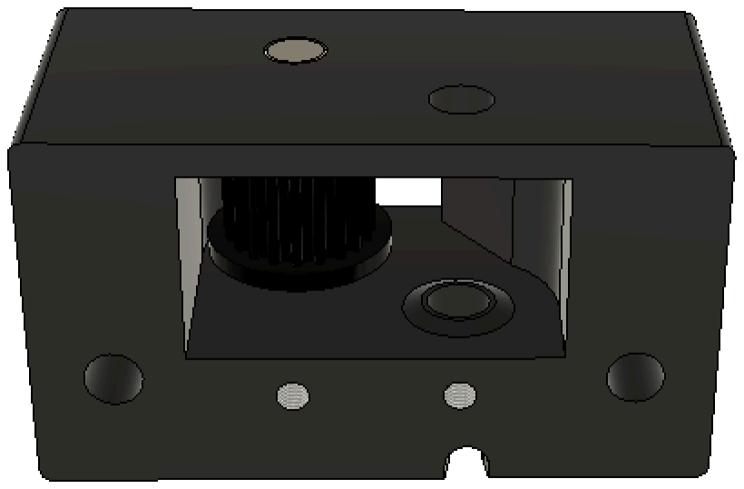
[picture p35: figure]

Repeat this for the other locaon with another GT2 20t Idler Pulley with 5mm Bore and another 5x25 Linear Sha.

Install an M3x6mm set screw into the deeper M3 threaded hole. Tighten the set screw unl secure with the M5x25mm linear sha.

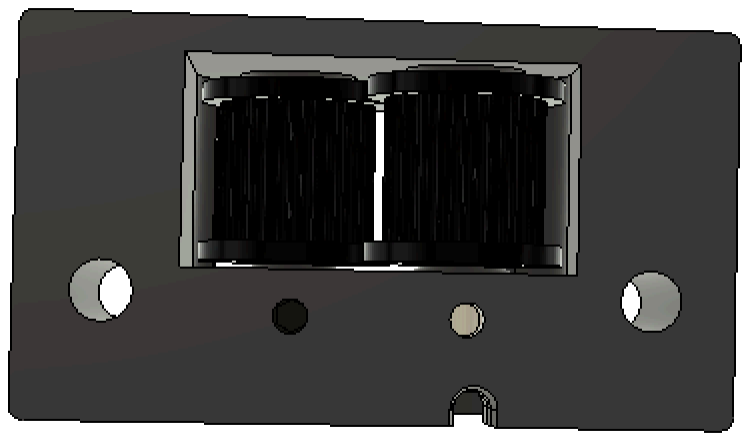
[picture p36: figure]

Install an M3x5mm set screw into the other M3 threaded hole. Tighten the set screw unl secure with the M5x25mm linear sha.

Press a 4x9x4 Bearing into printed Z-Axis Tackle Roller.

Coat an M4x10mm SHCS with medium strength thread locker. Put the M4x10mm SHCS through the assembled Z-Axis Tackle Roller and into the heat insert of the main printed part. Tighten the M4x10mm SHCS unl snug, then back it off unl the assembled tackle roller turns easily.

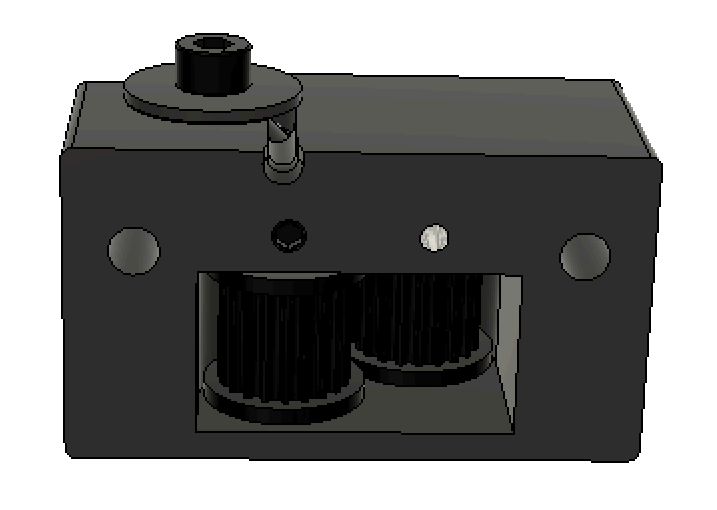
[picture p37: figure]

Snap the printed Z-Axis Belt Idler Right Part 02 CE onto the top of the Z-Axis Belt Idler Assembly.

Now repeat these steps to build the le side Z-Axis Idler Assembly.

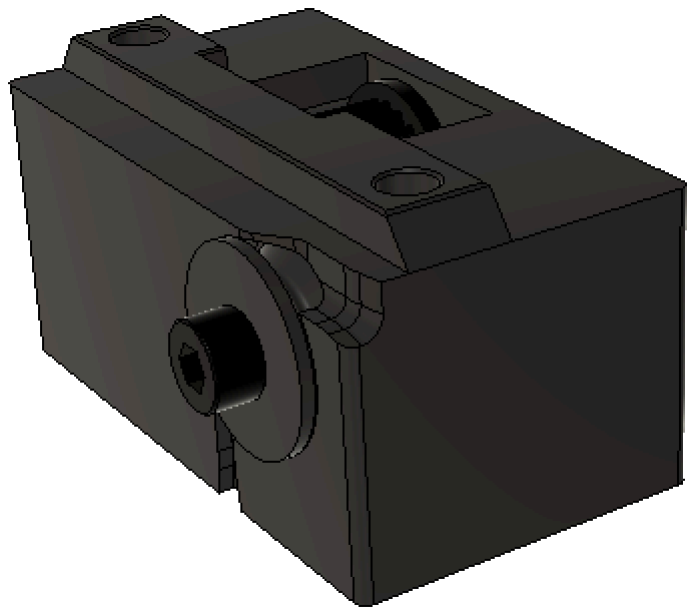
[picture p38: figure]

Install two M4 Slot 8 roll-in nuts into the underside of the right 420mm 4040 extrusion as shown.

Place the right Z-Axis Belt Idler assembly on the underside of the right 420mm 4040 extrusion and align the holes of the M4 Slot 8 roll-in nuts with the holes in the assembly. Loosely aach two M4x35mm SHCS through the Z-Axis Belt Idler assembly into the M4 Slot 8 roll-in nuts.

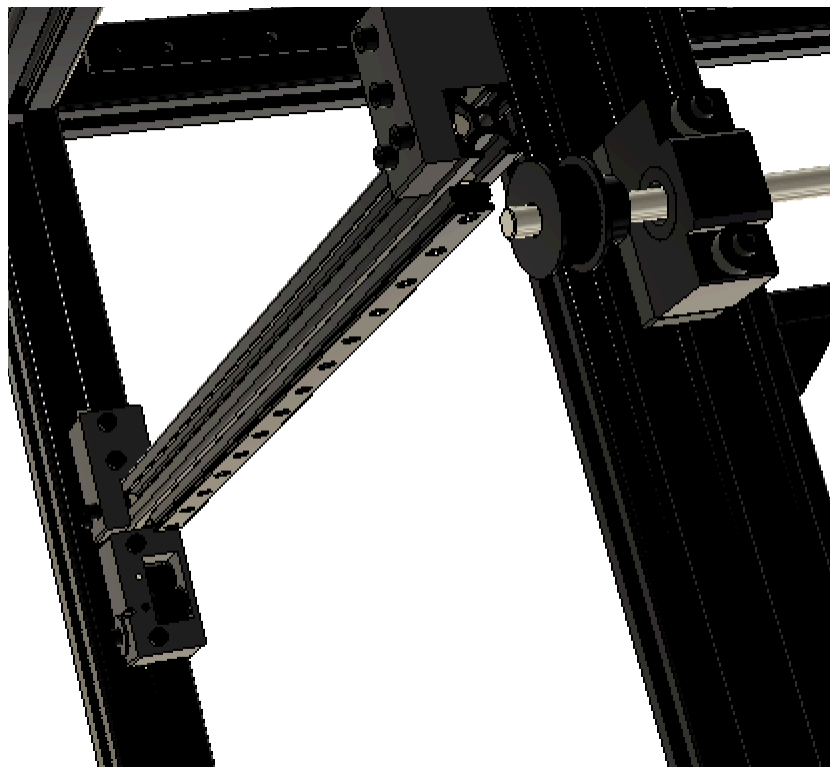
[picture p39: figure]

Place the printed Z-Axis Idler Pulley Installaon Tool with the ribbed side toward the underside of the 420mm 4040 extrusion. Slide the Z-Axis Idler Pulley assembly unl it is flush with the printed Installaon Tool and the printed tool is flush to the 395mm 4040 extrusion. Fully ghten the two M4x35 SHCS.

Remove the printed Installaon tool. Repeat the previous steps to install the le Z-Axis Belt Pulley Idler assembly. Turn the frame upright. Congratulaons, you have completed the Z-Axis Moon Assembly.

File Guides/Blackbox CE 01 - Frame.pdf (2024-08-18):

### Frame

# BLACKBOX CE

DOCUMENTATION VERSION 1

Version | Notes

## 1 Initial Release

# Change Log

# Blackbox CE Mechanical Assembly: 01. Frame

### Authored by Daniel Darms

## Description Metric Tape Measure or Meter Stick Electric Drill Hand Tap Wrench Hex Wrenches Blue Painters Tape Carpenters Square Reamers Threadlocker Soldering Iron with Heatset insert tip

# Tools

# Parts

QTY | Description | Material | Ver | Link
1 | Print_Z-Axis_Support_Installation_Tool_(146.311)_CE | PLA | 1
1 | Print_Y-Axis_Linear_Rail_Installation_Tool_(16.5) | PLA | 1
3 | Print_MGN12_Alignment_Block_4040 | PLA | 1
2 | Print_4040_Corner_Bracket_Installation_Tool_CE | PLA | 1
1 | Print_Z-Axis_Left_Linear_Rail_Installation_Tool_(10)_CE | PLA | 1
1 | Print_Z-Axis_Right_Linear_Rail_Installation_Tool_(20)_CE | PLA | 1
3 | Print_MGN12_Alignment_Block_2020 | PLA | 1
1 | Print_Z-Axis_Support_Bracket_Top_CE | >=ABS | 1
1 | Print_Z-Axis_Support_Bracket_Bottom | >=ABS | 1
4 | Print_Corner_Bracket_Top_CE | >=ABS | 1
12 | Print_Corner_Bracket_Lock_CE | >=ABS | 1
4 | Print_Corner_Bracket_Bottom_CE | >=ABS | 1
4 | Print_Corner_Bracket_Bottom_Lock_CE | >=ABS | 1
4 | Pint_TPU_Foot_CE | TPU | 1

# Printed Parts

## Step 1 – Preparation

Find a flat surface which will be large enough to hold your frame. The assembled frame dimensions are 570mm x 520mm. Lay out all the 4040 extrusions for idenficaon. There are three lengths: 395mm (x4), 420mm (x2), and 470mm (x4). The 470mm extrusions will define the front (and back) of the machine. The printed parts will take the majority of labor hours (hopefully for your printer) involved in the build. For the frame secon, the Support Installaon Tool and the Alignment Blocks may be printed in a less expensive material such as PLA. The four Boom Corner Brackets also incorporate the machine foot and is recommended to print with cubic subdivision infill paern at 100%. All through holes in the printed parts need to be cleaned with a reamer of the same size. Your MGN12 linear rails come with the MGN12H cartridges pre-installed. These cartridges are matched to the rails and should not be removed. There are over 60 small ball bearings inside of each MGN12H cartridge that can easily fall out and become lost if the cartridge comes off the rail or even if half or less of the cartridge moves past the end of the rail. It is best to secure the rail in place with blue painters tape to prevent unfortunate accidents. Both M3 and M4 heat set inserts are used in this guide. Most soldering iron installaon kits for heat set inserts have a different p for M3 and M4 inserts. You will need to let the iron cool aer installing inserts of one size before switching to the other installaon p to connue with the other size.

## NOTE:

Test the fit of Print_Corner_Bracket_Installation_Tool with the end of an extrusion before getting started.

This part is meant to fit tightly and thus may need special attention if your readiness print test was imperfect!

This tool is responsible for constraining each extrusion as a given corner bracket is tightened to avoid any

twisting. Failure to use this tool may result in a frame that measures square but suffers from skew.

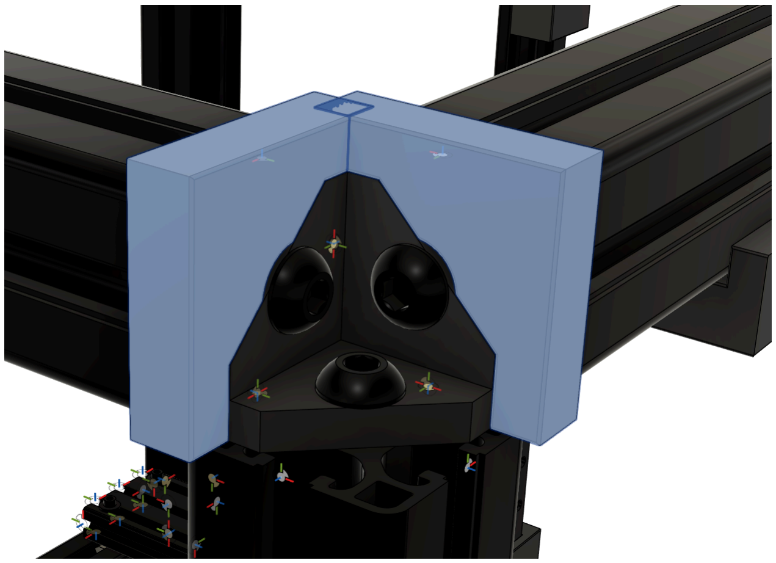
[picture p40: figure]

## Step 2 – Upper Frame

Start with a 4040 extrusion of 470mm. Aach a 4040 corner bracket using a M8x25mm BHHS. Do not fully ghten the screws for now, you will fully ghten the screws a bit later.

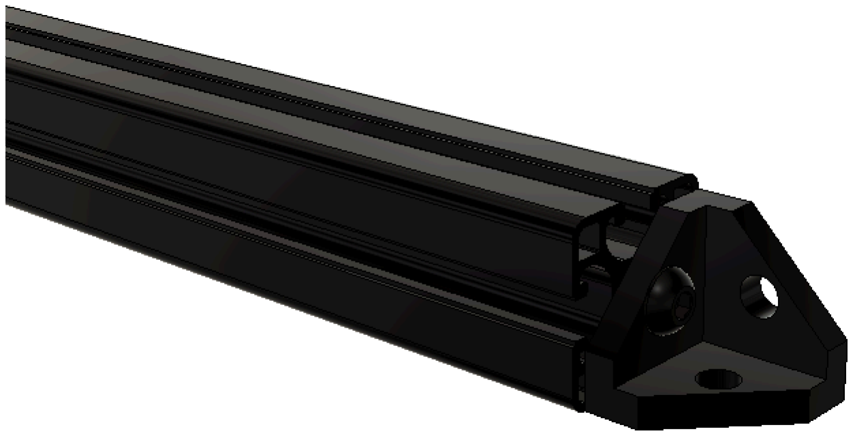
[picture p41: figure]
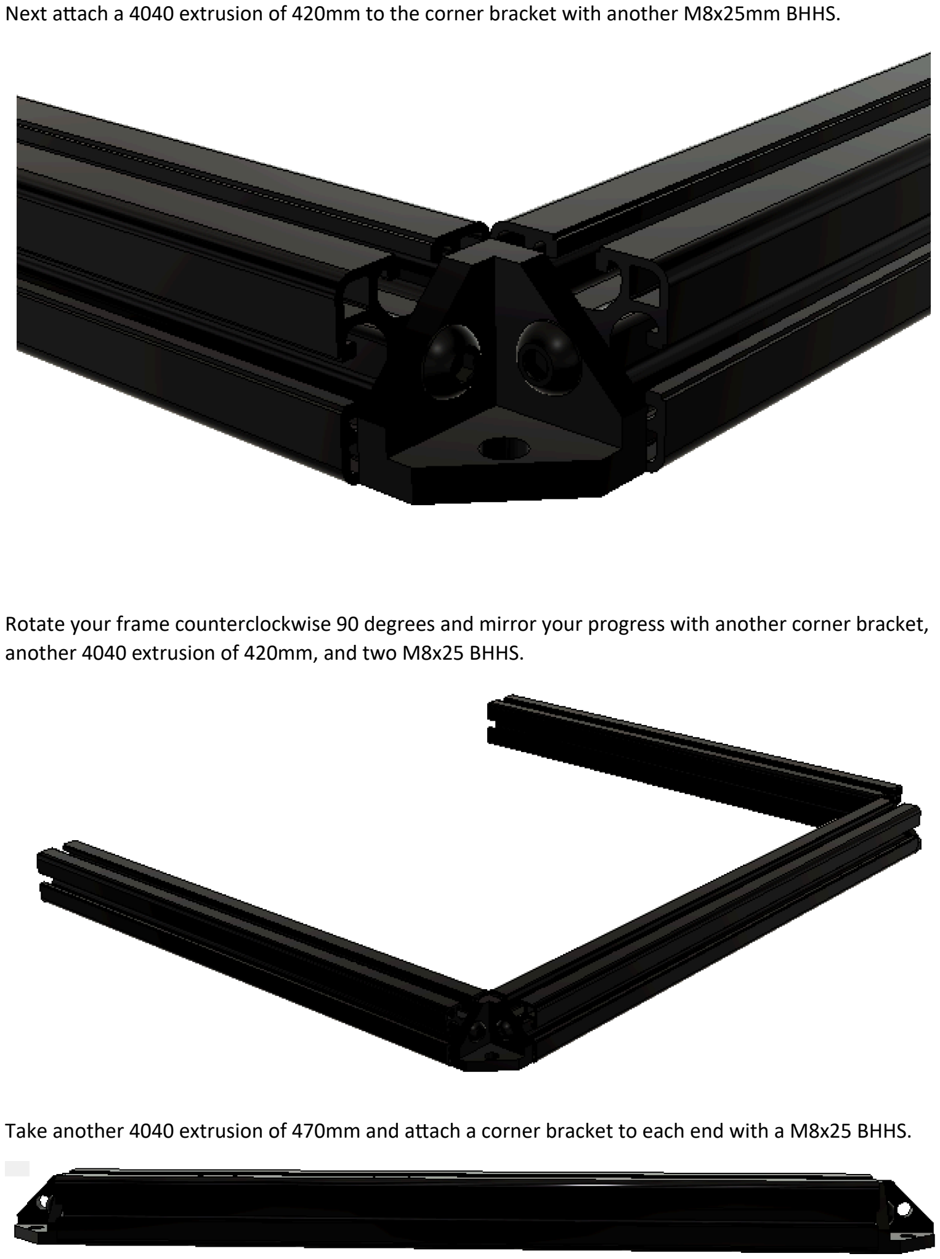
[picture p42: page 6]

Next aach a 4040 extrusion of 420mm to the corner bracket with another M8x25mm BHHS.

Rotate your frame counterclockwise 90 degrees and mirror your progress with another corner bracket, another 4040 extrusion of 420mm, and two M8x25 BHHS.

Take another 4040 extrusion of 470mm and aach a corner bracket to each end with a M8x25 BHHS.

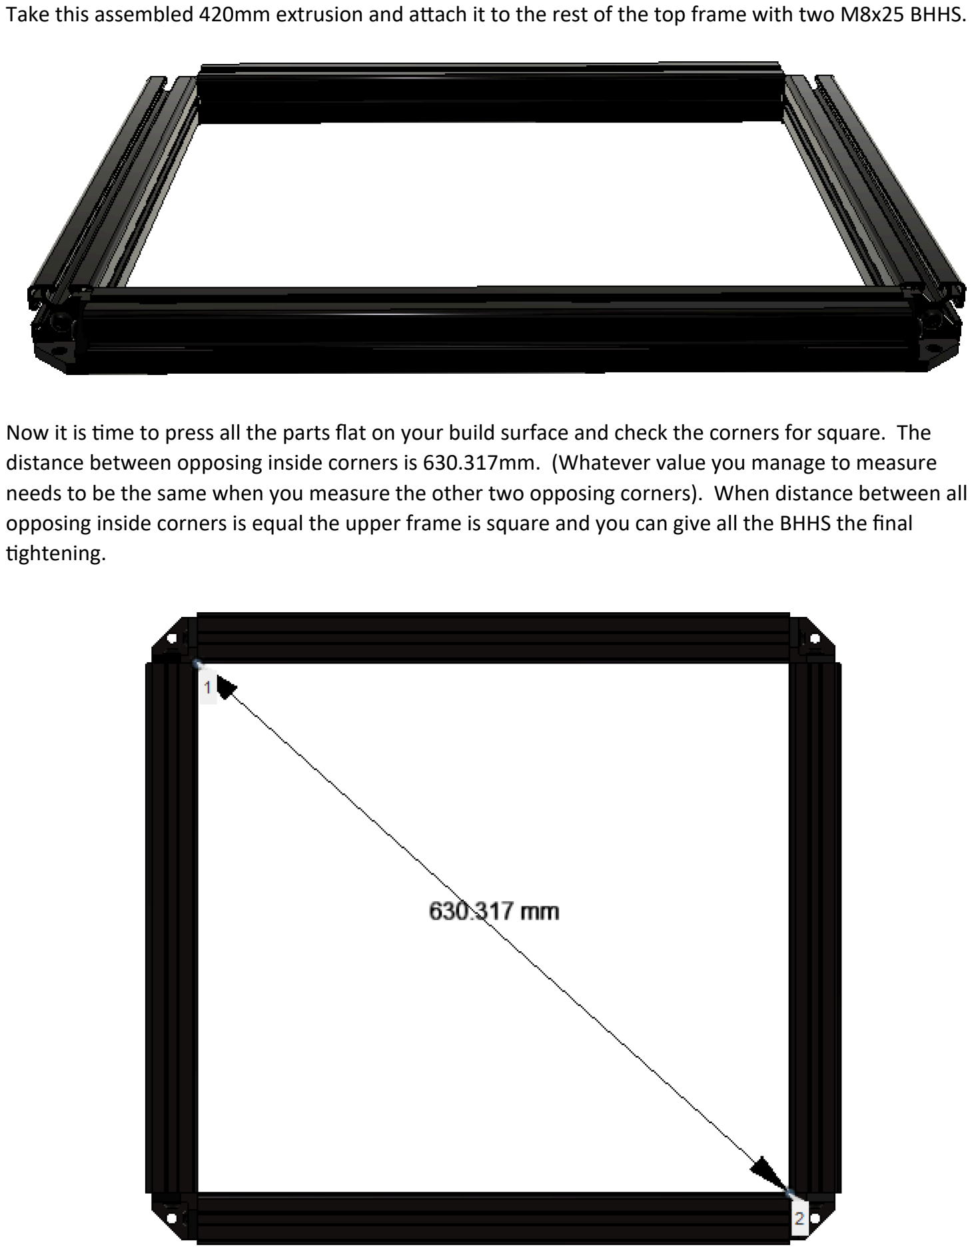
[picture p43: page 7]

Take this assembled 420mm extrusion and aach it to the rest of the top frame with two M8x25 BHHS.

Now it is me to press all the parts flat on your build surface and check the corners for square. The distance between opposing inside corners is 630.317mm. (Whatever value you manage to measure needs to be the same when you measure the other two opposing corners). When distance between all opposing inside corners is equal the upper frame is square and you can give all the BHHS the final ghtening.

## Step 3 – Side Frames

Turn the assembled upper frame onto one of the 420mm frame extrusions. Aach a 4040 extrusion of 395mm to a corner bracket using a M8x25mm BHHS.

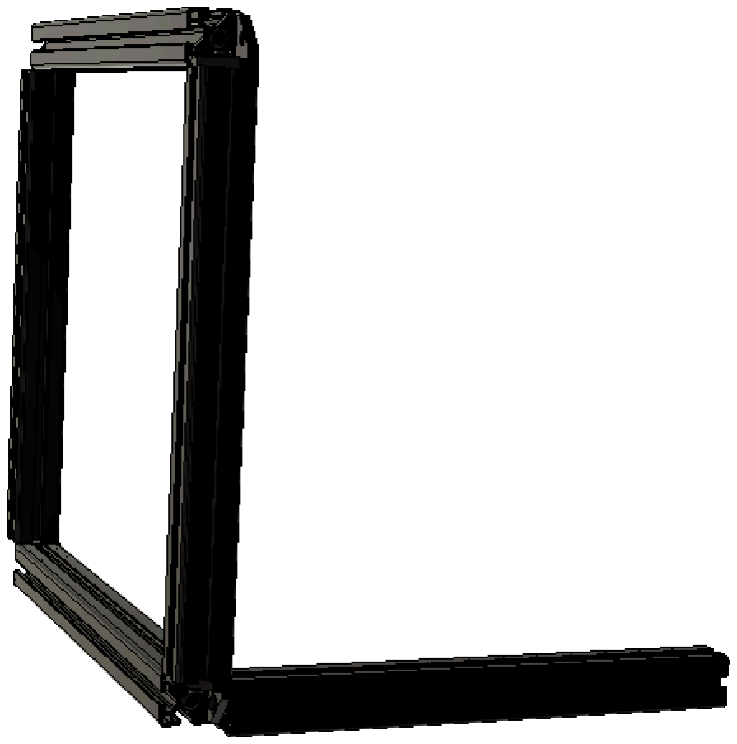
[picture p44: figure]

Aach another 395mm extrusion to the other lower corner bracket of the upper frame with a M8x25mm BHHS.

Take another 4040 extrusion of 470mm and aach a corner bracket to each end with a M8x25 BHHS.

Aach this assembled 470mm extrusion to the boom of the two 395mm extrusions using two M8x25 BHHS.

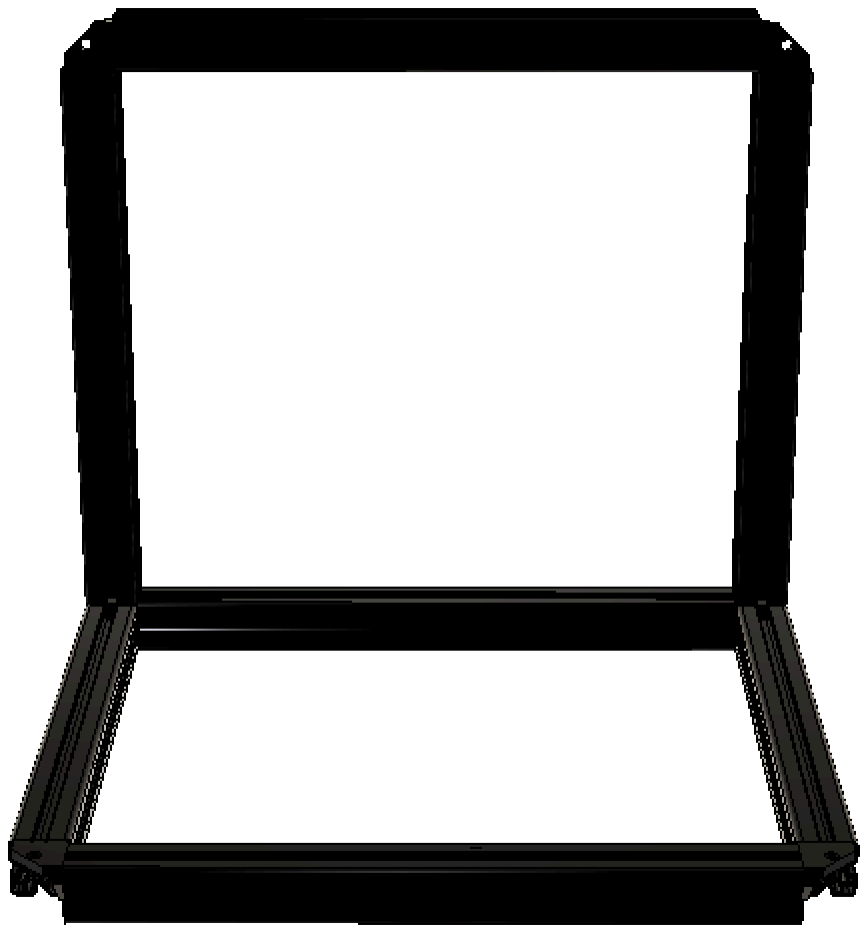
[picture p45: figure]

Using a carpenters square, check that the angle between the side frame and the upper frame is 90 degrees.

And check that the distance between opposing inside corners of side frame is 613.942mm. (Whatever value you manage to measure needs to be the same when you measure the other two opposing corners). Give these screws for the side frame a final ghten.

Now build the remaining side in a similar fashion using the remaining 470mm extrusion, two corner brackets and four M8x25mm BHHS. Be certain to check for square and equal distances as stated above. When finished, ghten all screws to final torque.

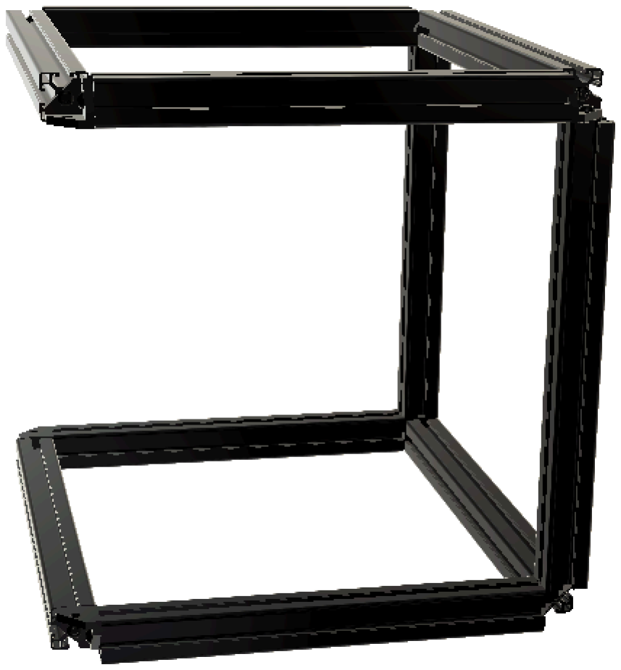
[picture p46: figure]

## Step 4 – Bottom Frame

Now turn the parally completed frame upright with one of the side openings facing you. This will become the front side. We are now going to aach the two 2060 extrusions to the side frames. (If your 2060 extrusions have three holes on each end, we are going to only use the outer two holes. Future 2060 extrusions will only come with two drilled holes per end). Place two M4 Slot 8 roll-in nuts in the top slot of the lower extrusion near a corner.

Repeat the inseron of the M4 Slot 8 roll-in nuts for the other three corners.

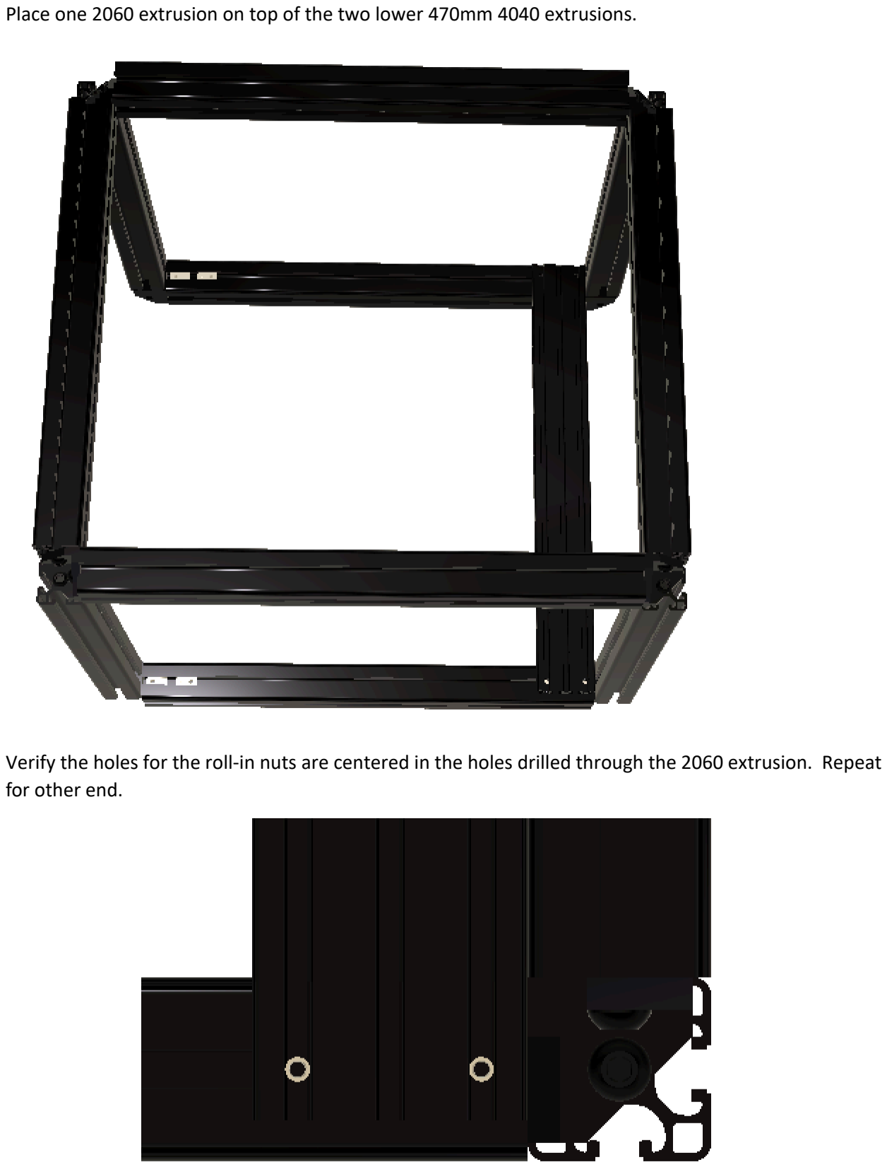
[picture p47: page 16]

Place one 2060 extrusion on top of the two lower 470mm 4040 extrusions.

Verify the holes for the roll-in nuts are centered in the holes drilled through the 2060 extrusion. Repeat for other end.

Insert a M4x30mm SHCS through a M4 fender washer and insert through one of the holes of the 2060 extrusion then fasten to the M4 Slot 8 roll-in nut. Repeat for the three other holes of the 2060 extrusion. Check that the 2060 extrusion is flush against the two 395mm 4040 extrusions.

Repeat this process for the other side with the remaining 2060 extrusion, 4 M4x30 SHCS, and 4 M4 fender washers.

Now to verify frame is square, measure the distance between the outer faces of the lower 470mm 4040 extrusions. The distance should be 500mm at each end. Adjust if necessary while keeping the 2060 extrusions flush with the vercal 395mm 4040 extrusions. Tighten all the M4 screws of the 2060 extrusions. Note: The 2060 extrusions have a light profile and cannot handle over-ghtening. Any excessive ghtening into a roll-in nut will cause the nut to deform the extrusion it is housed in.

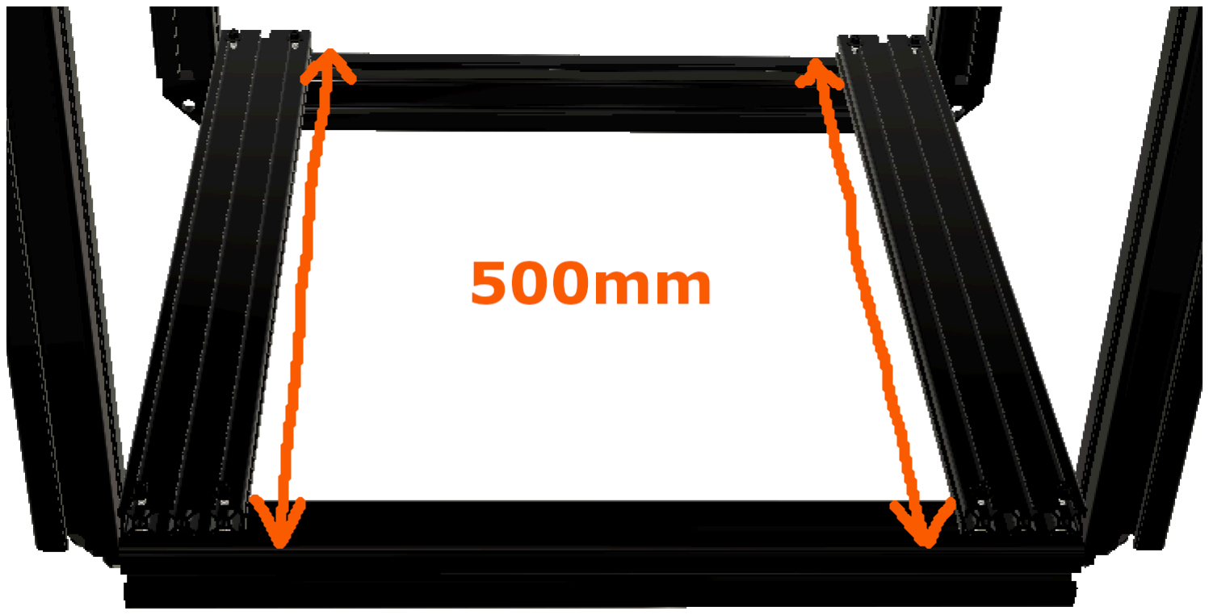
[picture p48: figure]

## Step 5 – Linear Rails

Look at your frame and choose one of the sides with the 470mm extrusions to be the front and orient this side facing you. For the rest of the guide, printed parts and assembly contexts will use the nomenclature of front, back, le, and right. Mulple parts which aach to the same side will be designated as top and boom. Lay the frame down onto its front face. Locate one of the 335mm MGN12 rails and remove the blue painters tape if installed in the preparaon secon. Be careful not to let the MGN12H carriage slide to the end or off the rail as you move it around during installaon. Insert eight M3 Slot 8 roll-in nuts into the le front 395mm 4040 extrusion as shown. The exact posions will be realized as the MGN12 rail is secured.

Place the MGN12 rail assembly onto the 395mm 4040 extrusion and secure it with three printed 4040 MGN12 Alignment Blocks.

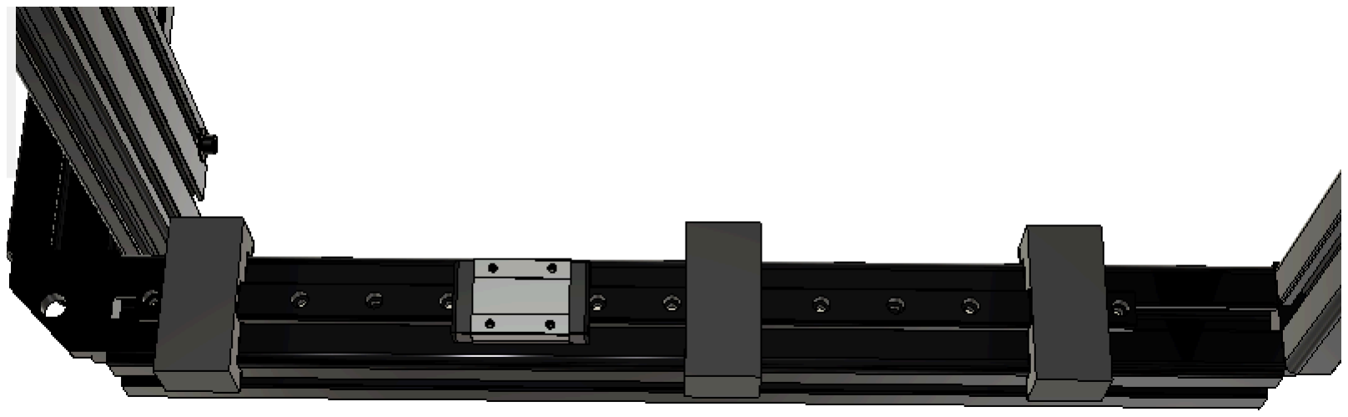
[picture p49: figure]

Laid out this way, all the holes used to secure the MGN12 rail to the 395mm 4040 extrusion are accessible. It is likely that your M3 Slot 8 roll-in nuts are not aligned with the proper holes at first. It is easiest to correct this by moving the MGN12 rail up or down (le and right by aspect of picture) unl the hole through one of the ends of the MGN12 rail matches up with the threads of the corresponding M3 Slot 8 roll-in nut. One aligned, loosely screw an M3x14 SHCS through the MGN12 rail into the M3 Slot 8 roll-in nut. Refer to the picture below with all screws aached to verify you are using the correct hole paern. Aer you have loosely aached the first M3x14 SHCS, move the MGN12 rail again unl the next prescribed hole lines up with its corresponding M3 Slot 8 roll-in nut. Repeat this unl all eight screws are loosely aached. You will likely need to slide the MGN12H cartridge out of the way to facilitate access to some of the holes.

Now that all the M3x14 SHCS are loosely screwed into their proper holes, install the Print_Z-Axis_Le_Linear_Rail_Installaon_Tool_(10)_CE into the Slot 8 of the 4040 extrusion. Slide the MGN12 rail so the boom of the rail is flush to the printed Installaon Tool and the printed Installaon tool is flush to the 4040 Corner Bracket.

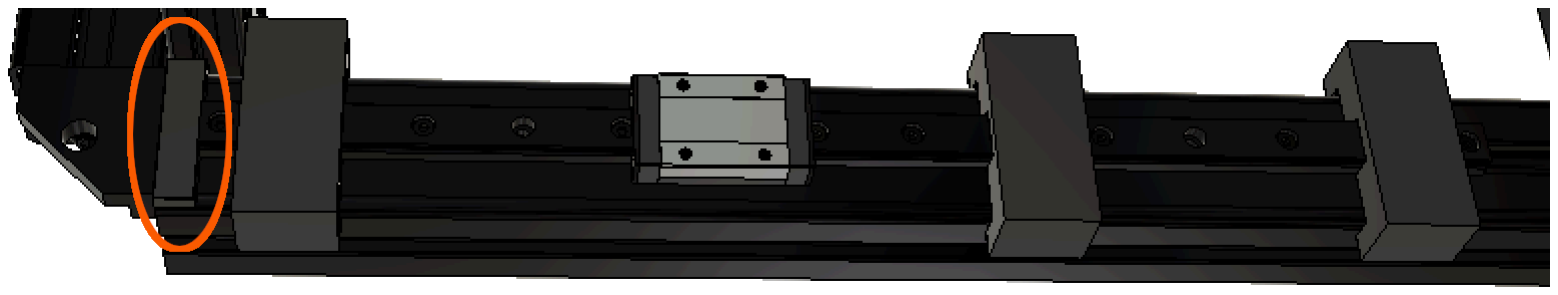
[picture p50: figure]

Tighten all the M3x14mm SHCS. Remember not to overghten these screws to prevent damage to the slot profile in the 4040 extrusion. The 4040 slot profile may also be damaged if the 4040 alignment blocks are not used to hold the MGN12 rail in place as the screws are ghtened. Apply some blue painters tape to the MGN12H cartridge to keep it from moving as you connue to assemble the frame. Remove the 4040 MGN12 alignment blocks and the printed Linear Rail Installaon Tool. Rotate the frame 180 degrees so the rear side is facing your work surface. Repeat all above steps to secure another 335mm MGN12 assembly to the other 395mm extrusion. Rotate your frame upright. The installed MGN12 rails should appear on the le side of your machine as depicted below.

Rotate the frame so the top is facing work surface and front side facing you. Locate one of the 400mm MGN12 rails and remove the blue painters tape if installed in the preparaon secon. Be careful not to let the MGN12H carriage slide to the end or off the rail as you move it around during installaon. Insert nine M3 Slot 8 roll-in nuts into the boom face of the front 470mm 4040 extrusion as shown. The exact posions will be realized as the MGN12 rail is secured.

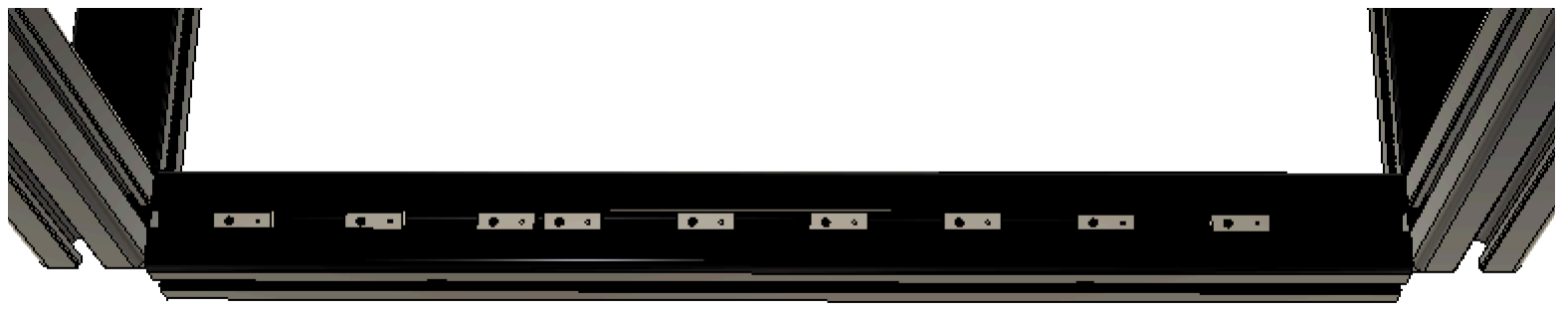
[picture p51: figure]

Place the MGN12 rail assembly onto the 470mm 4040 extrusion and secure it with three printed 4040 MGN12 Alignment Blocks.

Laid out this way, all the holes used to secure the MGN12 rail to the 470mm 4040 extrusion are accessible. It is likely that your M3 Slot 8 roll-in nuts are not aligned with the proper holes at first. It is easiest to correct this by moving the MGN12 rail le and right unl the hole through one of the ends of the MGN12 rail matches up with the threads of the corresponding M3 Slot 8 roll-in nut. One aligned, loosely screw an M3x14 SHCS through the MGN12 rail into the M3 Slot 8 roll-in nut. Refer to the picture below with all screws aached to verify you are using the correct hole paern. Aer you have loosely aached the first M3x14 SHCS, move the MGN12 rail again unl the next prescribed hole lines up with its corresponding M3 Slot 8 roll-in nut. Repeat this unl all nine screws are loosely aached. You will likely need to slide the MGN12H cartridge out of the way to facilitate access to some of the holes.

Now that all the M3x14 SHCS are loosely screwed into their proper holes, install Print_Y-Axis_Linear_Rail_Installaon_Tool_(16.5) onto the 395mm 4040 extrusion. Slide the MGN12 rail so the right end (le end for perspecve of picture) of the rail is flush to the printed installaon tool and the printed installaon tool is flush to the right 395mm 4040 extrusion.

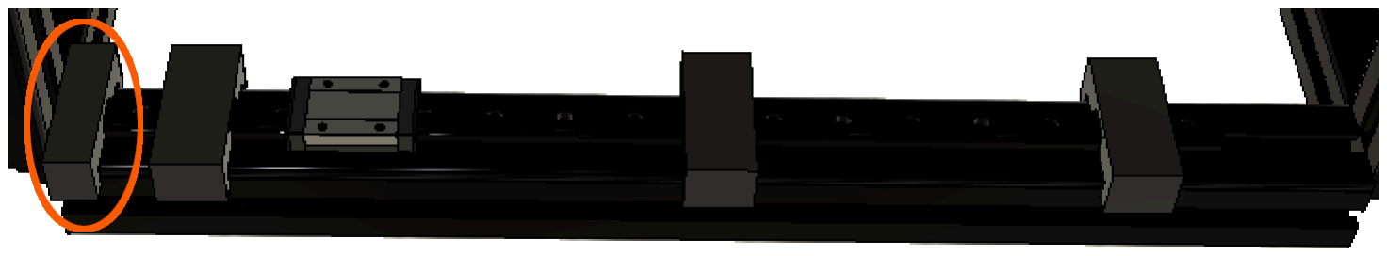
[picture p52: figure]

Tighten all the M3x14mm SHCS. Remember not to overghten these screws to prevent damage to the slot profile in the 4040 extrusion. The 4040 slot profile may also be damaged if the 4040 alignment blocks are not used to hold the MGN12 rail in place as the screws are ghtened. Apply some blue painters tape to the MGN12H cartridge to keep it from moving as you connue to assemble the frame. Remove the 4040 MGN12 alignment blocks and the printed Installaon Tool. Rotate the frame 180 degrees so the top side is facing your work surface and the rear side is facing you. Repeat all above steps to secure another 400mm MGN12 assembly to the other 470mm extrusion. Rotate your frame upright. The installed MGN12 rails should appear on the underside of the top frame as depicted below.

Move the frame aside and place the 2020 extrusion of 395mm in front of you. Locate the remaining 335mm MGN12 rail and remove the blue painters tape if installed in the preparaon secon. Be careful not to let the MGN12H carriage slide to the end or off the rail as you move it around during installaon. Insert eight M3 Slot 6 roll-in nuts into the 395mm 2020 extrusion as shown. The exact posions will be realized as the MGN12 rail is secured.

Place the MGN12 rail assembly onto the 395mm 2020 extrusion and secure it with three printed 2020 MGN12 Alignment Blocks.

Laid out this way, all the holes used to secure the MGN12 rail to the 395mm 2020 extrusion are accessible. It is likely that your M3 Slot 6 roll-in nuts are not aligned with the proper holes at first. It is easiest to correct this by moving the MGN12 rail up or down (le and right by aspect of picture) unl the hole through one of the ends of the MGN12 rail matches up with the threads of the corresponding M3 Slot 6 roll-in nut. Once aligned, loosely screw an M3x8 SHCS through the MGN12 rail into the M3 Slot 6 roll-in nut. Refer to the picture below with all screws aached to verify you are using the correct hole paern. Aer you have loosely aached the first M3x8 SHCS, move the MGN12 rail again unl the next prescribed hole lines up with its corresponding M3 Slot 6 roll-in nut. Repeat this unl all eight screws are loosely aached. You will likely need to slide the MGN12H cartridge out of the way to facilitate access to some of the holes.

Now that all the M3x8 SHCS are loosely screwed into their proper holes, install Print_Z-Axis_Right_Linear_Rail_Installaon_Tool_(20)_CE into the Slot 6 of the 2020 extrusion. Hold the printed Installaon Tool flush to the boom of the 2020 extrusion then slide the MGN12 rail so the boom end (le end for perspecve of picture) of the rail is flush to the printed Installaon Tool.

Tighten all the M3x8mm SHCS. Remember not to overghten these screws to prevent damage to the slot profile in the 2020 extrusion. The 2020 slot profile may also be damaged if the 2020 alignment blocks are not used to hold the MGN12 rail in place as the screws are ghtened. Apply some blue painters tape to the MGN12H cartridge to keep it from moving as you connue to assemble the frame. Remove the 2020 MGN12 alignment blocks and the printed Installaon Tool.

## Step 6 – Z-Axis Support

Insert two M4 Slot 6 roll-in nuts into the 395mm 2020 extrusion as shown. The exact posions will be realized later.

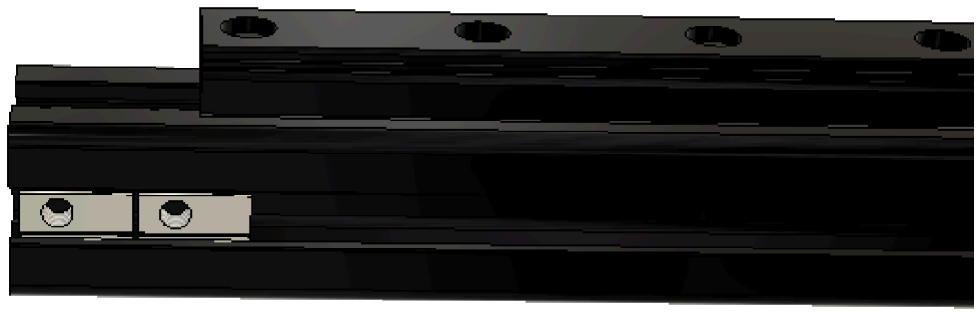
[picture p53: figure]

Place the printed part Z-Axis_Support_Bracket_Boom as shown. It is likely that your M4 Slot 6 roll-in nuts are not aligned with the proper holes at first. It is easiest to correct this by moving the printed part up or down unl the hole through one of the ends of the printed part matches up with the threads of the corresponding M4 Slot 6 roll-in nut. One aligned, loosely screw an M4x16 SHCS through the printed part into the M4 Slot 6 roll-in nut. Aer you have loosely aached the first M4x16 SHCS, move the printed part again unl the other hole lines up with its corresponding M4 Slot 6 roll-in nut. Stand the extrusion up and slide the printed part unl it is flush with the boom of the 395mm 2020 extrusion. Tighten all the M4x16 SHCS.

Insert two M4 Slot 6 roll-in nuts into the other end of the 395mm 2020 extrusion as shown. The exact posions will be realized later.

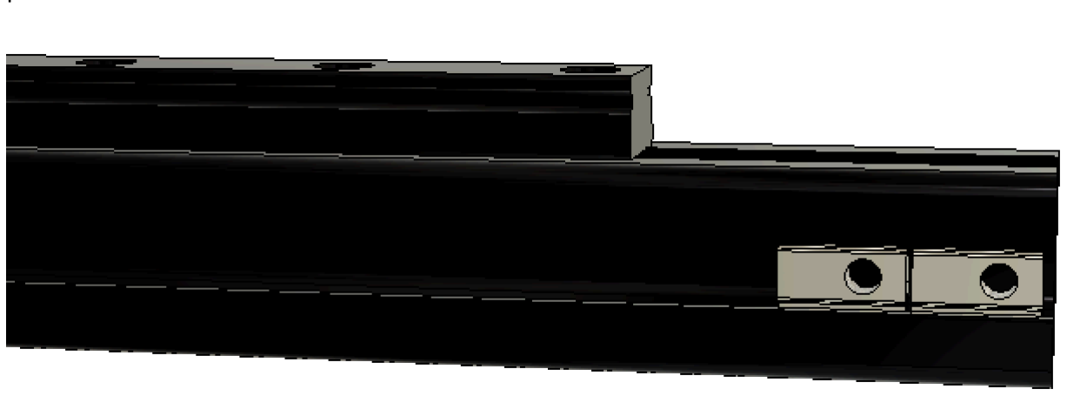
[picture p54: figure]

Place the printed part Z-Axis_Support_Bracket_Top as shown. It is likely that your M4 Slot 6 roll-in nuts are not aligned with the proper holes at first. It is easiest to correct this by moving the printed part up or down unl the hole through one of the ends of the printed part matches up with the threads of the corresponding M4 Slot 6 roll-in nut. One aligned, loosely screw an M4x16 SHCS through the printed part into the M4 Slot 6 roll-in nut. Aer you have loosely aached the first M4x16 SHCS, move the printed part again unl the other hole lines up with its corresponding M4 Slot 6 roll-in nut. Stand the extrusion up and slide the printed part unl it is flush with the top of the 395mm 2020 extrusion. Tighten all the M4x16 SHCS.

The Z-Axis Support Assembly should appear as depicted below.

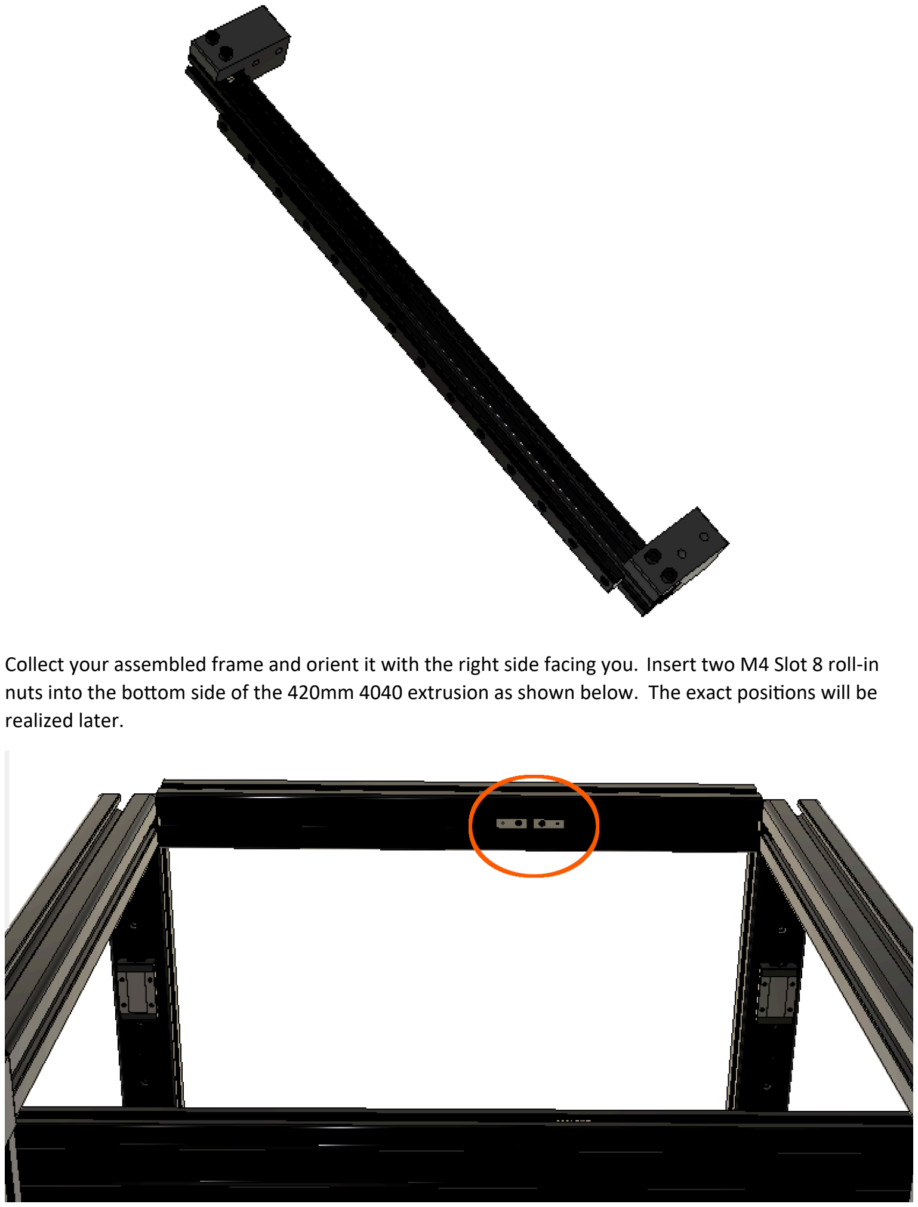
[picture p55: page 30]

Collect your assembled frame and orient it with the right side facing you. Insert two M4 Slot 8 roll-in nuts into the boom side of the 420mm 4040 extrusion as shown below. The exact posions will be realized later.

Insert two M4 Slot 6 roll-in nuts into the right side of the 482mm 2060 extrusion as shown below. The exact posions will be realized later.

Place the assembled Y-Axis Support onto the frame as shown. It is likely that your M4 Slot 8 roll-in nuts and M4 Slot 6 roll-in nuts are not aligned with the proper holes at first. It is easiest to correct this by moving the top of the assembly from front to back (le and right by aspect of picture) unl the hole through one of the ends of the printed part matches up with the threads of the corresponding M4 Slot 8 roll-in nut. Once aligned, loosely screw an M4x35 SHCS through the upper printed part into the M4 Slot 8 roll-in nut. Aer you have loosely aached the first M4x35 SHCS, move the top of the assembly again unl the other hole lines up with its corresponding M4 Slot 8 roll-in nut. Loosely install the other M4x35 SHCS. Now move the boom of the assembly from front to back (le and right by aspect of picture) unl the hole through one of the ends of the printed part matches up with the threads of the corresponding M4 Slot 6 roll-in nut. Once aligned, loosely screw an M4x35 SHCS through the lower printed part into the M4 Slot 6 roll-in nut. Aer you have loosely aached the first M4x35 SHCS, move the boom of the assembly again unl the other hole lines up with its corresponding M4 Slot 6 roll-in nut. Loosely install the other M4x35 SHCS. Place the printed tool Z-Axis Support Installaon onto the rear 395mm 4040 extrusion. The tab on the printed tool goes into the 8mm slot of the 4040 extrusion. Slide the top of the Z-Axis support assembly unl it is flush with the tool. Tighten all the top M4x35mm SHCS.


Move the printed tool to boom of the rear 395mm 4040 extrusion. Again, the tab on the printed tool goes into the 8mm slot of the 4040 extrusion. Slide the boom of the Z-Axis support assembly unl it is flush with the tool. The tool does not line up as well as it does when used at the top of the assembly. Be certain to keep the end of the tool with the tab flush and perpendicular with the 395mm 4040 extrusion to ensure proper distance is achieved. Tighten all the boom M4x35mm SHCS. Remove the tool. Your assembled frame should resemble the picture below.

## Step 7 – Corner Brackets


Move the frame aside. Locate the 12 printed Corner Bracket Lock parts. An M3 heat set insert will be installed flush into one side of six of these, and the other side of the other six. When completed, your inserts should resemble the below picture.

Orient your frame to face an upper corner. Install one of each type of printed Corner Bracket Lock into the 4040 extrusions as shown below.

Insert a printed Corner Bracket Top as shown.

Insert an M3x10mm SHCS into the recessed hole of the printed Corner Bracket Top, then push the screw in by hand with enough force to move the printed Corner Bracket Lock unl the screw is fully seated.


Using the angled end of your M3 hex wrench, ghten the M3x10 SHCS while pressing on the printed Corner Bracket Lock unl the M3x10 SHCS pulls the printed Corner Bracket Lock flush to the printed Corner Bracket Top and is ght. Repeat the process with another M3x10 SHCS on the other face of the printed Corner Bracket Top.

Repeat the above step for the other three top frame corners. With the top corner brackets installed turn your assembled frame upside down and orient the boom front right corner toward you. The lower brackets use the same parts, however, they are assembled differently per orientaon. The front right and rear le corner brackets are assembled the same way. This is true about the front le and rear right corner brackets. We will start by collecng the four printed Corner Bracket Boom Lock. We will insert an M3 heat set insert into the outer hole of each lock.


Locate the four printed Corner Bracket Boom parts and insert an M4 heat set insert into the center hole of one side for two of them and the other side for the other two. The result should resemble the picture below.

The two printed brackets to the le will aach to the Rear Le and the Front Right. The two printed brackets to the right will aach to the Front Le and Rear Right.


Turn all of the printed Corner Bracket Boom parts over and insert an M4 heat set insert into the center hole.

Locate and install a Print_TPU_Foot_CE onto each corner foot using (4 total) M4x10mm FHHS

Place the appropriate Corner Bracket Lock into the 4040 extrusion as shown.

NOTE: Going forward - images in this guide are shown WITHOUT the TPU foot pad!

Insert the printed Corner Bracket Boom which has an M4 insert which will show through the open hole in the Aluminum Corner Bracket.

Place an M3x10 SHCS fully into the recessed pocket of the Corner Bracket Boom.


Line up the M3 heat set insert in one of the printed Corner Bracket Boom Lock parts with the M3x10 SHCS you just installed into the printed Corner Bracket Boom. Using the angled end of your hex wrench, ghten the M3x10 SHCS allowing the screw to pull the printed Corner Bracket Boom Lock flush to the printed Corner Bracket Boom. Be certain the keyed post on the printed Corner Bracket Boom Lock is properly aligned so it goes through the Aluminum Corner Bracket.

When the printed Corner Bracket Boom Lock is flush and ght to the printed Corner Bracket Boom, install an M4x25 FHHS through the center of the printed Corner Bracket Boom Lock and into the printed Corner Bracket Boom, then fully ghten.


Insert an M3x10 SHCS in the recessed hole of the printed Corner Bracket Boom on the opposite face. Fully press the screw in by hand moving the printed Corner Bracket Lock.

Put pressure on the printed Corner Bracket Lock as you ghten the M3x10 SHCS with the angled end of a hex wrench. As you ghten the M3x10 SHCS the printed Corner Bracket Lock will move toward the printed Corner Bracket Boom. Connue to ghten unl these printed parts are flush and ght.


Repeat these steps for the following three boom corners of the fame. Congratulaons! Your basic frame is now complete and assembled.

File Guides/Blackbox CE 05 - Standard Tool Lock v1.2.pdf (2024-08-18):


Standard Tool Lock.

# BLACKBOX CE

DOCUMENTATION VERSION 1.2

Version | Notes

## 1 Initial Release 1.1 New tool lock index and moved Z switch 1.2 Changed Trigger Magnet size to metric, changed worm gear set screw to 4mm

# Change Log

# Blackbox CE Mechanical Assembly: 05. Standard Tool Lock

### Authored by Daniel Milton Darms

## Description Cyanoacrylate Glue (Super Glue / Krazy Glue) Electric Drill Hex Wrenches Threadlocker Soldering Iron with Heatset insert tip Tweezers

# Tools

QTY | Description

1 Blackstop Hall Effect Endstop Sensor 3 DIN912_M2_6mm_SHCS 3 DIN912_M3_6mm_SHCS 1 DIN912_M3_8mm_SHCS 2 DIN912_M3_25mm_SHCS 1 DIN912_M3_40mm_SHCS 1 DIN916_M3_2mm_Set_Screw 1 DIN7991_M3_35_FHHS 1 ISO7380_M2_5mm_BHHS 1 Lock_Motor_Nema8_LDO 1 M3x4.6x4 Heat Set Insert 1 Neodymium_Cylinder_Magnet_3mm 1 Worm1:40_4mmBore 1 WormWheel1:40_5mmBore
QTY | Description | Material | Ver | Link
1 | Print_Standard_Lock_Motor_Installation_Tool_(1.7) | PLA | 1
1 | Print_Tool_Lock_Mount_Standard | >= ABS | 21
1 | Print_ToolLockIndex_V2 | >= ABS | 2

# Parts

# Printed Parts

## Step 2 – Standard Tool Lock

Locate a DIN7991_M3_35_FHHS and fully secure in the locaon shown below.

## Step 1 – Preparation

It is best to lay out all the required hardware idenfied in each step. The Installaon Tools may be printed in a less expensive material such as PLA.


Locate Print_Standard_Lock_Motor_Installaon_Tool_(1.7).


Snap the printed installaon tool onto LockMotor_Nema8_LDO as shown.


Locate the Worm1:40_4mmBore and slide it onto the motor sha unl it is flush with the printed installaon tool.


Rotate the worm unl the hole for the grub screw is located over the flat part of the motor sha. Coat a DIN916_M3_2mm_Set_Screw with medium strength thread locker and secure the worm to the motor sha. Start by securing the set screw facing the flat of the motor sha. As this screw ghtens, wiggle the worm to assure the flat end of the set screw mates flush with the flat of the NEMA 8 motor sha. Keep the base of the worm ght with the printed Installaon Tool to set the proper pulley height. Tighten the M3x2mm set screw completely.


Remove the printed installaon tool. Locate Print_Tool_Lock_Mount_Standard and install a M3_4.6x4mm_Heat_Set_Insert as shown.


Place the NEMA 8 motor assembly into the printed standard lock mount and center the motor in the cradle. Pay aenon to the wiring harness connector orientaon.


Secure the motor to the mount with three DIN912_M2_8mm_SHCS as shown.


Place the standard mount assembly onto the printed X-Bracket assembly as shown.


Secure the standard lock assembly to the printed X-Bracket assembly with two DIN912_M3_25mm_SHCS


Install and fully ghten a DIN912_M3_40mm_SHCS into the locaon shown.


Install and fully ghten a DIN912_M3_8mm_SHCS into the locaon shown.

Locate the WormWheel1:40_5mmBore and place it on the t-lock sha as shown. Push the worm wheel flush to the printed standard lock mount and orient the grub screw hole to face the flat of the end of t-lock sha.

Check that the worm wheel is centered to the worm and then coat a DIN916_M4_5mm_Set_Screw with medium strength thread locker and secure the worm wheel to the t-lock sha. Start by securing the set screw facing the flat of the t-lock sha. As this screw ghtens, wiggle the worm wheel to assure the flat end of the set screw mates flush with the flat of the t-lock motor sha. Tighten the M3x5mm set screw completely.


Locate Print_ToolLockIndex_V2 and secure a Neodymium_Cylinder_Magnet_3mm into the locaon shown with CA adhesive. NOTE: The magnet should be flush to the back side of the printed part. Note that the back side of this part has a raised feature for centering.


Place the printed lock index assembly onto the end of the t-lock sha. Secure the lock index to the worm wheel with (1) ISO7380_M2_5mm_BHHS as shown. NOTE: The final posion of the lock index will be set later during the commissioning of the machine.


Fasten the BlackStop to the standard lock assembly with a DIN912_M3_6mm_SHCS as shown.


Install (2) DIN912_M3_6mm SHCS in the remaining two fastening locaons.


## Congratulaons! You have completed all the steps for the assembly of the Standard

Remote Lock.

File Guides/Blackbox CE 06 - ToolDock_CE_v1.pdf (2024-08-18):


### Tool Dock

# BLACKBOX CE

DOCUMENTATION VERSION 1

Version | Notes

## 1 Initial Release 1.1 Wiper Assembly changes, PCB standoffs

# Change Log

# Blackbox CE Mechanical Assembly: 06. Tool Dock

## Description 2 Part Epoxy or CA Glue Epoxy Mixing stick or Toothpick Hand Tap Wrench Hex Wrenches Heat Sinking Paste M3x0.5mm Tap Reamers Threadlocker Soldering Iron with Heatset insert tip Electric Drill

# Tools

# Parts

QTY | Description | Material | Ver | Link
1 | Print_ToolBank_Installation_Tool | PLA | 1
5 | Print_ToolWiper_part_01 | >=ABS | 1
5 | Print_ToolWiper_part_04 | >=ABS | 1
5 | Print_ToolWiper_part_02 | >=ABS | 1
10 | Print_ToolWiper_part_03 | >=ABS | 1
5 | Print_ToolDock | >=ABS | 2
5 | Print_ToolDockSpacer_Part_01 | >=ABS | 2
5 | Print_ToolDockSpacer_Part03_CE | >=ABS | 1
5 | Print_ToolDockSpacer_Part_02 | >=ABS | 1
5 | Print_ToolDockWireGuide | >=ABS | 1

# Printed Parts

## Step 2 – Tool Docks

Locate the tool dock printed parts shown below. Use an M3x0.5 tap to create threads at these 2 locaons. Be sure to tap all the way down and into the 4mm bores to which they intersect.

## Step 1 – Preparation

Do not overghten any hardware going into a roll-in nut installed to a 2010 or 2020 extrusion to prevent deformaon. The lengths of hardware are not substutable, and a shorter length will prevent proper hold strength while a longer length will deform the 2010 or 2020 profile. You must request or acquire the proper hardware specified in the guide. Hardware going through printed parts can be substuted only with adjustments made to the associated printed part.


Install M3 heat set inserts (6) in the following locaons:

Firstly, two here:


Flip the dock and install the remaining heat set inserts here:


Install a 5x10mm Neodymium magnet here. Note that we will be repeang these steps to build up all 5 tool docks. It is important to keep the polarity of the magnets in a consistent direcon during assembly. This will keep you from tool docking issues later in the build. For now, we only need to ensure that the polarity is consistent across all docks. It can be helpful to mark the “top” of the (5) 5x10 magnets at this me. Be sure each magnet is fully seated into the printed dock. Once installed and seated the magnet should have a snug fit. Since there is no retenon mechanism other than a fricon fit for these magnets, some 2-part epoxy can be used to further secure them in case of a loose fit.

Before Using Epoxy if necessary: See the first page of Step 4!


Install (2) 4mmx30mm shas as shown:

Note that the final posion of these shas may be adjusted later in the building process. Nominally though they will begin flush with the back-side of the dock.

NOTE: It is important that these shas be perpendicular to the face of the printed part when finished with this step. If your print tolerance requires opening the hole diameter to accept the shas be sure to use ONLY a squarely driven 4mm reamer included in the kit.


Install and seat (2) M3x6mm set screws into the now threaded bores and ghten to secure the 4x30 shas. The set screws travel well into the printed part, so a longer reach hex key may be required. The below view should help visualize the funcon of the set screws.


Install a printed tool dock wire guide and secure with an M3x8 FHHS.


Repeat step 1 four addional mes for each remaining tool dock.

Posion (2) M3 Nylon washers on the dock

Install a Tool Dock PCB using (2) M3x6mm SHCS

## Step 2 – Tool Wiper Assemblies (For FDM Tools)

Locate one of the below printed parts and install (4) M3 heat set inserts in the shown locaons. Note that the (2) inside inserts are to be installed from the back side of the printed part. Be sure that they ulmately are located flush with the inside face of the printed part!


Locate the below printed part and install a Silicone Leak Blocker into the channel as shown.

NOTE: This part is located in an FDM Tool Hardware Kit!

Install onto the main nozzle wiper printed part and fasten using (2) M3x12FHHS.


Locate the below printed part and install (2) M3 heat set inserts in these locaons:

Locate (2) Silicone Nozzle Wipers and (2) Print_Nozzle_Wiper_Part03. Each wiper will be separated by the two printed parts as shown in the stack below. Secure the stack loosely using (2) M3x8 SHCS.

Note that the height of the nozzle wipers will be set later in the build process. Be careful not to over ghten the M3x8 SHCS to avoid deforming the silicone wipers.

Secure the nozzle wiper sub assembly to the main nozzle wiper assembly using (2) M3x10 SHCS

NOTE: This part is located in an FDM Tool Hardware Kit!


## Repeat this process for as many FDM Tool Head you will be installing on

your Blackbox.

## Step 3 – Tool Dock Spacer Assemblies


Locate a printed Tool Dock Spacer housing and install an M3 heat set insert at the shown locaon.

Locate the shown printed part and snap into place as pictured below.

Locate Print_ToolDockSpacer_Part02 and temporarily (loosely) secure with an M3x35 FHHS. This piece will eventually be used to secure a spring wire that helps manage the wire hoops to each equipped tool.


Repeat this step 4 addional mes.

## Step 4 – Full Sub-Assembly

Locate idle tool cooler and orient as shown.


Place each tool dock assembly against the idle tool cooler. The 5x10 magnet is the only contact point unl the next step. The magnets should pass into the tool cooler with a slight press fit. If required, the tool cooler can be reamed to 5mm.

VERY IMPORTANT: - All of the magnets should be either flush with the face of the tool cooler or slightly below flush. Any magnets that extend past the surface of the tool cooler will cause a loss of conducve heat transfer on docked tools. If one or more magnets are too far exposed, now is the me to press them further or diagnose the cause of the extra height.



Fix all tool wiper assemblies (and thus docks) to the idle tool cooler using (10) M3x16 SHCS and loosely ghten. These fasteners will be fully ghtened at a later step.

Locate 1 of the two water blocks and install (2) BSPT tube fings as shown.

Insert two 64mm lengths of tubing into each fing. Achieving perfect lengths and square cut ends is not necessary. The sealing surface for these fings is an O-ring seal against the OD of the tubing. Ensure that no cut debris enters the tubing before installaon. A sharp razor blade can be used to achieve clean cuts, but always pracce good safety when working with blades. Be sure the tube is fully seated in each fing!


Before performing this next step, it is important to clean any residual dust and/or machining oils from the (back) face of the idle tool cooler bar. Isopropyl alcohol and acetone are great for this purpose, but please use gloves, lung, and eye protecon in a well-venlated area when using these chemicals. They are also highly flammable!

NOTE: Be sure to remove the plasc protecon film from the copper face of the water block if equipped! Leaving this in place will result in near-zero cooling ability for the idle tool bar.

Deposit a pea-sized amount of thermal compound to the middle of the copper face of the water block. Install and secure as shown using (4) M3x20 SHCS at the indicated locaons. Ensure the orientaon of the cooler block is correct by confirming that the hose and fings are parallel to the X axis of the machine.

These fasteners should be ghtened uniformly and without high torque to avoid warping the cooler itself.


Install (10) 4040 M4 T nuts into the le upper inside extrusion as shown.

Working with the enre tool bank sub-assembly, capture each of the remaining Tool Dock Spacer sub-assemblies using (10) M4x30 SHCS.


A second view of the fully assembled Tool Dock Assembly ready for installaon.

Move each T-nut into its esmated final posion manually before proceeding. Loosely fasten the subassembly to the frame using the two far corners first.


Loosely ghten the remaining 8 fasteners aer making any final micro adjustments to the Tnuts that accept them.

Locate the Print_ToolDock_Installaon_Tool pictured below:

Place the printed tool between the tool bank assembly and upper forward 4040 extrusion. Slide the Tool Dock assembly and printed tool forward (toward front of machine) unl no gap remains. Fully ghten all Tool Bank screws. Finally, fully ghten all the M3 SHCS that secure each Nozzle Wiper Assembly to each

tool dock. Remove printed tool.

## Congratulaons! You have completed all the steps for the assembly of

the Tool Dock.

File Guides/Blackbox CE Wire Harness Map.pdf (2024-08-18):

Main Harness Name | WIRE Name | Component A | Connector A | Component B | Connector B | Length (CM) Wire Gauge Color Marker Motion? | Connector Name

### Power Inlet

Jumper - Line | Power Inlet | Female Spade 6mm | Power Switch | Female Spade 4mm | 5 | 18 BRN | N
Jumper - Neutral | Power Inlet | Female Spade 6mm | Power Switch | Female Spade 4mm | 5 | 18 BLU | N
Line Wire | Power Switch | Female Spade 4mm | 24V Power Supply | Fork 4.3mm | 20 | 18 BRN | N
Neutral Wire | Power Switch | Female Spade 4mm | 24V Power Supply | Fork 4.3mm | 20 | 18 BLU | N
Ground Wire | Power Inlet | Female Spade 6mm | 24V Power Supply | Fork 4.3mm | 20 | 18 GN/YEL | N

### Solid State Relay

Line Wire (IN) | 24V Power Supply | Fork 4.3mm | SSR | Fork 4.3mm | 57 | 18 BRN | N
LINE Wire (LOAD) | SSR | Fork 4.3mm | Heated Bed WAGO | Bare Wire | 86 | 18 BRN | Y
Trigger + | Duet 3 6HC | Molex LG Pin 2 of 2 | SSR IN + | Fork 4.3mm | 42 | 24 RED | N | OUT_3
Trigger - | Duet 3 6HC | Molex LG Pin 1 of 2 | SSR IN - | Fork 4.3mm | 42 | 24 BLK | N | OUT_3

### Heated Bed WAGOs

Neutral 120V Wire | 24V Power Supply | Fork 4.3mm | Heated Bed WAGO | Bare Wire | 133 | 18 BLU | Y
Bed Thermistor + | Duet 3 6HC | Molex KK Pin 2 of 2 | Heated Bed WAGO | Bare Wire | 118 | 24 RED | Y | TEMP_3
Bed Thermistor - | Duet 3 6HC | Molex KK Pin 1 of 2 | Heated Bed WAGO | Bare Wire | 118 | 24 BLK | Y | TEMP_3

### SexBolt Offset Switch

Switch S | Sexbolt Switch | JST-XH Pin 1 of 2 | Duet 3 6HC | Molex KK Pin 2 of 5 | 141 | 24 GREEN | Y | IO_5_IN
Switch - | Sexbolt Switch | JST-XH Pin 2 of 2 | Duet 3 6HC | Molex KK Pin 3 of 5 | 141 | 24 BLK | Y | IO_5_IN

### 12V DC Converter

24V IN + | 24V Power Supply | Fork 4.3mm | 12V Converter | Fork 3.2mm | 67 | 18 RED | N
24V IN - | 24V Power Supply | Fork 4.3mm | 12V Converter | Fork 3.2mm | 67 | 18 BLK | N

### 5V DC Converter

24V IN + | 24V Power Supply | Fork 4.3mm | 12V Converter | Fork 3.2mm | 74 | 18 RED | N
24V IN - | 24V Power Supply | Fork 4.3mm | 12V Converter | Fork 3.2mm | 74 | 18 BLK | N
5V Out + | 5V Converter | Fork 3.2mm | Duet 3 6HC | Molex KK PIN 3 of 3 | 60 | 20 RED | N | 5V_EXT
5V OUT - | 5V Converter | Fork 3.2mm | Duet 3 6HC | Molex KK Pin 1 of 3 | 60 | 20 BLK | N | 5V_EXT

### Duet 3 6HC

24V IN + | 24V Power Supply | Fork 4.3mm | Duet 3 6HC | Fork 4.3mm | 91 | 18 RED | N | POWER_IN
24V IN - | 24V Power Supply | Fork 4.3mm | Duet 3 6HC | Fork 4.3mm | 91 | 18 BLACK | N | POWER_IN

### Duet 3 3HC

24V IN + | Duet 3 6HC | Fork 4.3mm | Duet 3 3HC | Fork 4.3mm | 39 | 18 RED | N | POWER_IN
24V IN - | Duet 3 6HC | Fork 4.3mm | Duet 3 3HC | Fork 4.3mm | 39 | 18 BLACK | N | POWER_IN

### Water Pump

Radiator Fan + | Duet 3 6HC | Molex KK Pin 2 of 2 | 6020 Fan | Microfit Connector Pin 1 of 4 | 50 | 24 RED | N | OUT_9
Radiator Fan - | Duet 3 6HC | Molex KK Pin 1 of 2 | 6020 Fan | Microfit Connector Pin 2 of 4 | 50 | 24 BLK | N | OUT_9
12V OUT + | 12V Converter | Fork 3.2mm | Water Pump + | Microfit Connector Pin 3 of 4 | 86 | 20 RED | N
12V OUT - | 12V Converter | Fork 3.2mm | Water Pump - | Microfit Connector Pin 4 of 4 | 86 | 20 BLK | N

### Display

| Display Data 1 | Duet 3 6HC | Molex KK Pin 2 of 5 | PanelDue | Molex KK Pin 4 of 4 | 62 | 24 GREEN | N | IO_0
| Display Data 2 | Duet 3 6HC | Molex KK Pin 3 of 5 | PanelDue | Molex KK Pin 2 of 4 | 62 | 24 BLACK | N | IO_0
| Display Data 3 | Duet 3 6HC | Molex KK Pin 4 of 5 | PanelDue | Molex KK Pin 3 of 4 | 62 | 24 BLUE | N | IO_0
| Display Data 4 | Duet 3 6HC | Molex KK Pin 5 of 5 | PanelDue | Molex KK Pin 1 of 4 | 62 | 24 RED | N | IO_0_5V_EXT

### Tool Docks

| Tool 0 Heater + | Duet 3 6HC | Molex LG Pin 2 of 2 | Tool Dock 0 | Microfit Receptacle Pin 4 of 4 | 136 | 20 RED | N | OUT_1
| Tool 0 Heater - | Duet 3 6HC | Molex LG Pin 1 of 2 | Tool Dock 0 | Microfit Receptacle Pin 1 of 4 | 136 | 20 BLACK | N | OUT_1
Tool 0 Thermistor + Duet 3 6HC | Molex KK Pin 1 of 2 | Tool Dock 0 | Microfit Receptacle Pin 2 of 4 | 136 | 24 RED | N | TEMP_0
| Tool 0 Thermistor - | Duet 3 6HC | Molex KK Pin 2 of 2 | Tool Dock 0 | Microfit Receptacle Pin 3 of 4 | 136 | 24 BLACK | N | TEMP_0
| Tool 1 Heater + | Duet 3 6HC | Molex LG Pin 2 of 2 | Tool Dock 1 | Microfit Receptacle Pin 4 of 4 | 141 | 20 RED | N | OUT_2
| Tool 1 Heater - | Duet 3 6HC | Molex LG Pin 1 of 2 | Tool Dock 1 | Microfit Receptacle Pin 1 of 4 | 141 | 20 BLACK | N | OUT_2
Tool 1 Thermistor + Duet 3 6HC | Molex KK Pin 1 of 2 | Tool Dock 1 | Microfit Receptacle Pin 2 of 4 | 141 | 24 RED | N | TEMP_1
| Tool 1 Thermistor - | Duet 3 6HC | Molex KK Pin 2 of 2 | Tool Dock 1 | Microfit Receptacle Pin 3 of 4 | 141 | 24 BLACK | N | TEMP_1
| Tool 2 Heater + | Duet 3 3HC | Molex LG Pin 2 of 2 | Tool Dock 2 | Microfit Receptacle Pin 4 of 4 | 131 | 20 RED | N | OUT_0
| Tool 2 Heater - | Duet 3 3HC | Molex LG Pin 1 of 2 | Tool Dock 2 | Microfit Receptacle Pin 1 of 4 | 131 | 20 BLACK | N | OUT_0
Tool 2 Thermistor + Duet 3 3HC | Molex KK Pin 1 of 2 | Tool Dock 2 | Microfit Receptacle Pin 2 of 4 | 131 | 24 RED | N | TEMP_0
| Tool 2 Thermistor - | Duet 3 3HC | Molex KK Pin 2 of 2 | Tool Dock 2 | Microfit Receptacle Pin 3 of 4 | 131 | 24 BLACK | N | TEMP_0
| Tool 3 Heater + | Duet 3 3HC | Molex LG Pin 2 of 2 | Tool Dock 3 | Microfit Receptacle Pin 4 of 4 | 136 | 20 RED | N | OUT_1
| Tool 3 Heater - | Duet 3 3HC | Molex LG Pin 1 of 2 | Tool Dock 3 | Microfit Receptacle Pin 1 of 4 | 136 | 20 BLACK | N | OUT_1
Tool 3 Thermistor + Duet 3 3HC | Molex KK Pin 1 of 2 | Tool Dock 3 | Microfit Receptacle Pin 2 of 4 | 136 | 24 RED | N | TEMP_1
| Tool 3 Thermistor - | Duet 3 3HC | Molex KK Pin 2 of 2 | Tool Dock 3 | Microfit Receptacle Pin 3 of 4 | 136 | 24 BLACK | N | TEMP_1
| Tool 4 Heater + | Duet 3 3HC | Molex LG Pin 2 of 2 | Tool Dock 4 | Microfit Receptacle Pin 4 of 4 | 141 | 20 RED | N | OUT_2
| Tool 4 Heater - | Duet 3 3HC | Molex LG Pin 1 of 2 | Tool Dock 4 | Microfit Receptacle Pin 1 of 4 | 141 | 20 BLACK | N | OUT_2
Tool 4 Thermistor + Duet 3 3HC | Molex KK Pin 1 of 2 | Tool Dock 4 | Microfit Receptacle Pin 2 of 4 | 141 | 24 RED | N | TEMP_2
| Tool 4 Thermistor - | Duet 3 3HC | Molex KK Pin 2 of 2 | Tool Dock 4 | Microfit Receptacle Pin 3 of 4 | 141 | 24 BLACK | N | TEMP_2
Enclosure Lighting | LED + (Stick1) | Duet 3 6HC | Molex KK Pin 1 of 2 | Light Stick 1 | JST XH Pin 1 of 2 | 144 | 20 RED | N | OUT_8
| LED - (Stick1) | Duet 3 6HC | Molex KK Pin 2 of 2 | Light Stick 1 | JST XH Pin 2 of 2 | 144 | 20 BLACK | N | OUT_8
| LED + (Stick2) | Light Stick 1 | JST XH Pin 2 of 2 | Light Stick 2 | JST XH Pin 1 of 2 | 61 | 20 RED | N
| LED - (Stick2) | Light Stick 1 | JST XH Pin 1 of 2 | Light Stick 2 | JST XH Pin 2 of 2 | 61 | 20 BLACK | N

### FDM Tool Hoops

Tool N Heater + | Tool Dock N | Microfit Receptacle Pin 4 of 4 | Tool Heater + | Microfit Receptacle Pin 1 of 2 | 70 | 20 RED | Y
Tool N Heater - | Tool Dock N | Microfit Receptacle Pin 1 of 4 | Tool Heater - | Microfit Receptacle Pin 2 of 2 | 70 | 20 BLACK | Y
Tool N Thermistor + Tool Dock N | Microfit Receptacle Pin 2 of 4 | Tool Thermistor + | Microfit Receptacle Pin 1 of 2 | 72 | 24 RED | Y
Tool N Thermistor - Tool Dock N | Microfit Receptacle Pin 3 of 4 | Tool Thermistor - | Microfit Receptacle Pin 2 of 2 | 72 | 24 BLACK | Y

### TOOL HEAD

E Motor Pair 1 | Duet 3 6HC | Molex LG Pin 1 of 4 | Extruder Motor | JST PH Pin 1 of 6 | 256 | 24 BLACK | Y | DRIVER_3
E Motor Pair 1 | Duet 3 6HC | Molex LG Pin 2 of 4 | Extruder Motor | JST PH Pin 6 of 6 | 256 | 24 BLUE | Y | DRIVER_3
E Motor Pair 2 | Duet 3 6HC | Molex LG Pin 3 of 4 | Extruder Motor | JST PH Pin 4 of 6 | 256 | 24 GREEN | Y | DRIVER_3
E Motor Pair 2 | Duet 3 6HC | Molex LG Pin 4 of 4 | Extruder Motor | JST PH Pin 3 of 6 | 256 | 24 RED | Y | DRIVER_3
T Motor Pair 1 | Duet 3 6HC | Molex LG Pin 1 of 4 | Tool Lock Motor | Microfit Connector Pin 1 of 4 | 256 | 24 RED | Y | DRIVER_4
T Motor Pair 1 | Duet 3 6HC | Molex LG Pin 2 of 4 | Tool Lock Motor | Microfit Connector Pin 2 of 4 | 256 | 24 BLUE | Y | DRIVER_4
T Motor Pair 2 | Duet 3 6HC | Molex LG Pin 3 of 4 | Tool Lock Motor | Microfit Connector Pin 3 of 4 | 256 | 24 GREEN | Y | DRIVER_4
T Motor Pair 2 | Duet 3 6HC | Molex LG Pin 4 of 4 | Tool Lock Motor | Microfit Connector Pin 4 of 4 | 256 | 24 BLACK | Y | DRIVER_4
X Endstop + | Duet 3 6HC | Molex KK Pin 5 of 5 | X Endstop | JST XH Pin 1 of 3 | 256 | 24 RED | Y | IO_1
X Endstop S | Duet 3 6HC | Molex KK Pin 4 of 5 | X Endstop | JST XH Pin 2 of 3 | 256 | 24 GREEN | Y | IO_1
X Endstop - | Duet 3 6HC | Molex KK Pin 3 of 5 | X Endstop | JST XH Pin 3 of 3 | 256 | 24 BLACK | Y | IO_1
Z Endstop S | Duet 3 6HC | Molex KK Pin 2 of 5 | Z Endstop | Microfit Connector Pin 1 of 2 | 256 | 24 GREEN | Y | IO_3
Z Endstop - | Duet 3 6HC | Molex KK Pin 3 of 5 | Z Endstop | Microfit Connector Pin 2 of 2 | 256 | 24 BLACK | Y | IO_3
TL Endstop + | Duet 3 6HC | Molex KK Pin 5 of 5 | Tool Lock Endstop | JST XH Pin 1 of 3 | 256 | 24 RED | Y | IO_4
TL Endstop S | Duet 3 6HC | Molex KK Pin 4 of 5 | Tool Lock Endstop | JST XH Pin 2 of 3 | 256 | 24 GREEN | Y | IO_4
TL Endstop - | Duet 3 6HC | Molex KK Pin 3 of 5 | Tool Lock Endstop | JST XH Pin 3 of 3 | 256 | 24 BLACK | Y | IO_4
Part Fan + | Duet 3 6HC | Molex KK Pin 2 of 2 | Part cooling Fan | Microfit Connector Pin 1 of 2 | 256 | 24 RED | Y | OUT_7
Part Fan - | Duet 3 6HC | Molex KK Pin 1 of 2 | Part cooling Fan | Microfit Connector Pin 2 of 2 | 256 | 24 BLACK | Y | OUT_7

### Y Endstop

Y Endstop + | Duet 3 6HC | Molex KK Pin 5 of 5 | Y Endstop | JST XH Pin 1 of 3 | 83 | 24 RED | N | IO_2
Y Endstop S | Duet 3 6HC | Molex KK Pin 4 of 5 | Y Endstop | JST XH Pin 2 of 3 | 83 | 24 GREEN | N | IO_2
Y Endstop - | Duet 3 6HC | Molex KK Pin 3 of 5 | Y Endstop | JST XH Pin 3 of 3 | 83 | 24 BLACK | N | IO_2

### B Motor

B Motor Pair 1 | Duet 3 6HC | Molex LG Pin 1 of 4 | B Motor | JST PH Pin 1 of 6 | 61 | 24 RED | N | DRIVER_0
B Motor Pair 1 | Duet 3 6HC | Molex LG Pin 2 of 4 | B Motor | JST PH Pin 3 of 6 | 61 | 24 BLUE | N | DRIVER_0
B Motor Pair 2 | Duet 3 6HC | Molex LG Pin 3 of 4 | B Motor | JST PH Pin 4 of 6 | 61 | 24 GREEN | N | DRIVER_0
B Motor Pair 2 | Duet 3 6HC | Molex LG Pin 4 of 4 | B Motor | JST PH Pin 6 of 6 | 61 | 24 BLACK | N | DRIVER_0

### A Motor

A Motor Pair 1 | Duet 3 6HC | Molex LG Pin 1 of 4 | A Motor | JST PH Pin 1 of 6 | 173 | 24 RED | N | DRIVER_1
A Motor Pair 1 | Duet 3 6HC | Molex LG Pin 2 of 4 | A Motor | JST PH Pin 3 of 6 | 173 | 24 BLUE | N | DRIVER_1
A Motor Pair 2 | Duet 3 6HC | Molex LG Pin 3 of 4 | A Motor | JST PH Pin 4 of 6 | 173 | 24 GREEN | N | DRIVER_1
A Motor Pair 2 | Duet 3 6HC | Molex LG Pin 4 of 4 | A Motor | JST PH Pin 6 of 6 | 173 | 24 BLACK | N | DRIVER_1

### Z Motor

Z Motor Pair 1 | Duet 3 6HC | Molex LG Pin 1 of 4 | Z Motor | JST PH Pin 1 of 6 | 17 | 24 RED | N | DRIVER_2
Z Motor Pair 1 | Duet 3 6HC | Molex LG Pin 2 of 4 | Z Motor | JST PH Pin 3 of 6 | 17 | 24 BLUE | N | DRIVER_2
Z Motor Pair 2 | Duet 3 6HC | Molex LG Pin 3 of 4 | Z Motor | JST PH Pin 4 of 6 | 17 | 24 GREEN | N | DRIVER_2
Z Motor Pair 2 | Duet 3 6HC | Molex LG Pin 4 of 4 | Z Motor | JST PH Pin 6 of 6 | 17 | 24 BLACK | N | DRIVER_2

### Raspberry Pi

| RPI 5V+ | 5V DC Converter | Fork 3.2mm | RPI | USB-C | 40 | 20 RED | N
| RPI 5V- | 5V DC Converter | Fork 3.2mm | RPI | USB-C | 40 | 20 BLK | N
AUX Cooling Fan | AUX Fan + | Duet 3 6HC | Molex KK Pin 2 of 4 | AUX fan | Microfit Connector Pin 1 of 2 | 85 | 24 RED | N | OUT_4
| AUX Fan - | Duet 3 6HC | Molex KK Pin 4 of 4 | AUX fan | Microfit Connector Pin 2 of 2 | 85 | 24 BLK | N | OUT_4
TOTAL WIRE (FEP) | TOTAL CM | TOTAL M | Total M +20%
Red 24ga | 2728 | 27.28 | 32.736
Black 24ga | 3125 | 31.25 | 37.5
Green 24ga | 1817 | 18.17 | 21.804
Blue 24ga | 825 | 8.25 | 9.9
Red 20ga | 1146 | 11.46 | 13.752
Black 20ga | 1146 | 11.46 | 13.752
Red 18ga | 271 | 2.71 | 3.252
Brown 18ga | 168 | 1.68 | 2.016
Black 18ga | 197 | 1.97 | 2.364
Blue 18ga | 158 | 1.58 | 1.896
Yel/Grn 18ga | 100 | 1 | 1.2

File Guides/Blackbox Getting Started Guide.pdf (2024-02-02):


Printed Parts Guide + Supplements

# BLACKBOX CE

DOCUMENTATION VERSION 1

Version | Notes
1 Initial Release

# Change Log

# Blackbox CE Getting Started Guide

# BEFORE YOU BEGIN

# Nozzle:

A 0.4mm nozzle is recommended for most parts, and some smaller parts were designed with this extrusion width in mind . If using a larger nozzle, ensure the resulting parts are strong and clean and accurate. Support settings and XY size compensation (AKA Horizontal expansion) should be tuned for your material prior to part printing.

# Material:

Considerations include rigidity, heat deformation resistance, and stress creep resistance. Most materials are viable (aside from PLA) Best results will come from a glass or carbon reinforced polymer. If a non-filled material is used, stay away from the more elastic plastics like PETG.

# Print Settings:

For best strength, print on the hotter end of your material temperature range. Use a low (or zero) part cooling fan speed where possible. Consider using the part cooling fan only on overhangs, support interfaces, and bridges.

# General Guidelines:

Blackbox parts are designed with printability in mind. Most parts will have an obvious orientation preference, and most are smaller in size. Still, printing in an enclosed build volume can help mitigate any warping with some materials.

Spend some time perfecting the profile used for your chosen filament. Pay close attention to any "Elephants Foot" during test prints. Also ensure that walls are flat with no "pimples" from over extrusion. Consider enabling and tuning linear advance to mitigate bulging sharp corners.

Blackbox has many printed parts and will require many days of printing along with 1.5-2.5 KG of material. The actual time and material amount will depend on your specific build.

# Materials & Settings

Below are the recommended specifications for FDM printing of Blackbox parts. All slicing programs will have these settings with slight variations in naming.

- LAYER HEIGHT: 0.2mm
- LINE WIDTH: 0.4mm
- INFILL: 40-50% (Grid, Gyroid, Honeycomb, Triangle or Cubic)
- PERIMETERS: 5-6
- TOP & BOTTOM SOLID LAYERS: 5-8

# Material Options

What we recommend:; PEEK; PETG, ABS (ABS+CF & GF), ASA; PLA (NOT RECCOMENDED); Higher Performance; Easier To Print

Carbon Fiber Filled PolyCarbonate (ABS Blend OK)

Why?
PC is a capable engineering material that can stand the test of time under the stresses of tightened fasteners and belts. The Carbon fiber adds rigidity to what would otherwise be a material prone to flex. The fiber fill also helps to avoid warping during/after printing and allows for cleaner bridging and overhangs.

# Tuning Your Filament Profile

As stated above, you should be sure to spend the time getting to know your filament of choice and how it interacts with your printer. Due to the diversity of filaments and machines, there is no one-size-fits-all standard that we can supply you with. Double check the performance of the following settings to have the best experience with the least amount of post- processing.

### 1. Temperature 2. Retraction 3. Print speeds and accelerations/jerk 4. Horizontal Expansion (XY Size Compensation) 5. Extrusion E-steps / Flow Rate 6. Support Z distance 7. Support density and interface 8. Bridging speed and flow rate 9. Linear Advance

Check out this lovely and free guide (https://teachingtechyt.github.io/) from TeachingTech for some helpful tips/tools on many of these topics.

# Introduction:

This guide will focus on the real-world results of your printer, slicer settings, and material. This test should be performed after most of your settings are well tuned. Before getting started here, print some calibration cubes, heat towers, retraction test pillars, ETC.

Once you are happy with the overall performance and quality of your printer and material combination, follow this guide to print your Blackbox Readiness Test Part (or BRTP for acronym enthusiasts)

# A look at what we are printing:

# Blackbox Printed Parts Readiness Test

Use this guide to assist in calibrating your printer and material in preparation for printing your Blackbox

Toolchanger parts.

## Download the STL here! (https://blackbox3d.xyz/stls/bbreadinesstest.3mf)

To confidently complete this guide, you will need a pair of measuring calipers (digital is fine) with a displayable

resolution of at least 0.1mm


# Overview:

This test print has been purpose designed to include the most challenging and critical features you will encounter while printing your parts. It includes the following features/challenges that you will find throughout your printing process:

### 1. Sharpest non-supported overhang present on Blackbox 2. Various vertical hole positions 3. Shaft/Bore tolerance locations 4. Supported overhangs 5. Critical X, Y, and Z dimensions 6. High retraction counts 7. Flat and curved surfaces

## General Slicing Settings:

Wall/Perimeter Count: 4
Number of Bottom Layers: 3 Number of Top layers: 3
Infill: 20%
Extrusion width: 0.4mm (Use only a 0.4mm nozzle for this print!) Supports: None

### Remember:

This guide will focus on confirming the results of your printer and profile tuning. It will offer some specific tips along the way but is not meant to be a comprehensive guide for tuning.

### Level of Importance: Critical

Measure at the shown location to confirm that your model height in the Z direction is identical to this value. Printed parts throughout Blackbox are designed to accept some level of deviation, but the printed parts for an FDM tool head will not align properly if not correct in the Z direction (as printed).

Pointers for a failed test print:

1. Ensure you are slicing all Blackbox models at 0.2mm layer heights, INCLUDING the first layer.
2. Ensure your printers Z axis moves freely and is adjusted properly.
3. Ensure your first layer height shows minimal (if any) elephant’s foot.
4. Ensure your extruders steps/mm are correct.
5. If all else is OK, you can consider adjusting your Z axis steps/mm.


### Level of Importance: Moderate

Measure at the shown location to confirm that your model’s width is equal to this dimension. Many factors go into tuning this dimension. Reference calibration cube guides for tips. NOTE: Avoid using horizontal expansion/XY size compensation to achieve this value.

Pointers for a failed test print:

1. Ensure your extruders steps/mm are correct.
2. Ensure your slicer’s flow rate is tuned.
3. Ensure you are not applying any horizontal expansion (AKA XY compensation) in your slicer.
4. If all else is OK, you can consider adjusting your Y axis steps/mm. NOTE: VERY rarely are Y steps/mm the proper way to adjust this value. See the teaching tech link above for help.


### Level of Importance: Moderate

Measure at the shown location to confirm that your model’s width is equal to this dimension. Many factors go into tuning this dimension. Reference calibration cube guides for tips. NOTE: Avoid using horizontal expansion/XY size compensation to achieve this value.

Pointers for a failed test print:

1. Ensure your extruders steps/mm are correct.
2. Ensure your slicer’s flow rate is tuned.
3. Ensure you are not applying any horizontal expansion (AKA XY compensation) in your slicer.
4. If all else is OK, you can consider adjusting your X axis steps/mm. NOTE: VERY rarely are X steps/mm the proper way to adjust this value. See the teaching tech link above for help.


### Level of Importance: Low

Elephant’s foot refers to a bulge of material caused by the “squishing” of the first layer of extrusion. Some slicers have compensation settings for this. This can be removed manually with post-processing but will distort assemblies combining multiple printed parts if left untouched.

1. 95% of the time this issue is caused by a layer height that is too low. If you are struggling for adhesion, use some build plate adhesive.
2. The layers following a too-squished first layer will also tend to bulge, especially if they are solid layers.
3. Some slicers have a compensation tick box for this. It is always best to adjust your bed level and height to mitigate this issue instead.


### Level of Importance: Moderate

Confirm the following dimensions of holes in the XY Plane. Typically, these holes will reflect the accuracy of the above X and Y dimensional tests. The 5mm hole shown should accept a 5mm dowel pin without excessive force. The 8mm bore shown should accept an 8mm OD Bondtech bearing without excessive force.

Pointers for a failed test print:

1. Test points #2 and #3 above will directly affect these features.
2. Over or under extrusion will also affect bore diameters.
3. Always prioritize the results from test points #2 and #3, bore holes can be reamed if too small.
4. If bores are too large, stop and remedy this now.


### Level of Importance: Low - Moderate

Visual Inspection – This feature will serve as the filament constraint near the Bondtech drive gears. Poor reproduction of this feature will affect your extrusion rate ceiling when printing flexibles.

Pointers for a failed test print:

1. Support roof interfaces help avoid sagging but can make support removal more difficult. This feature can print without support but will benefit from it.
2. Run your part cooling fan higher/faster when printing overhangs.


### Level of Importance: Moderate

Vertical holes are always difficult to produce accurately in FDM printing. Blackbox printed parts are designed with this in mind. We highly recommend reaming all vertical holes to size with the appropriately sized reamer. The red (3mm) holes should accept a 3mm dowel. The blue (stepped 4mm, 2mm) bore should measure appropriately.

Pointers for a failed test print:

1. Cura’s tree supports excel with vertical hole features. Give them a try if you need to.
2. Run your part cooling fan higher/faster when printing overhangs.
3. Conventional supports can be used too, but you’ll be aiming to find a balance between clean support and ease of removal.


# Features to Note:


While not necessarily needing to be measured, there are various other readiness indicators throughout this test print.

1. Bearing Depth Setter – Ensure it prints nicely and is not damaged during support removal.
2. Sharp Corners – Ensure sharp corners do not exhibit signs of bulging. Linear advance can be tuned to resolve this.

3. Supported holes – These areas will normally require reaming but ensure that any generated support material is easily removable.


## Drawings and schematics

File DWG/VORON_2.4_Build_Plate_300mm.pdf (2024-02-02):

A A

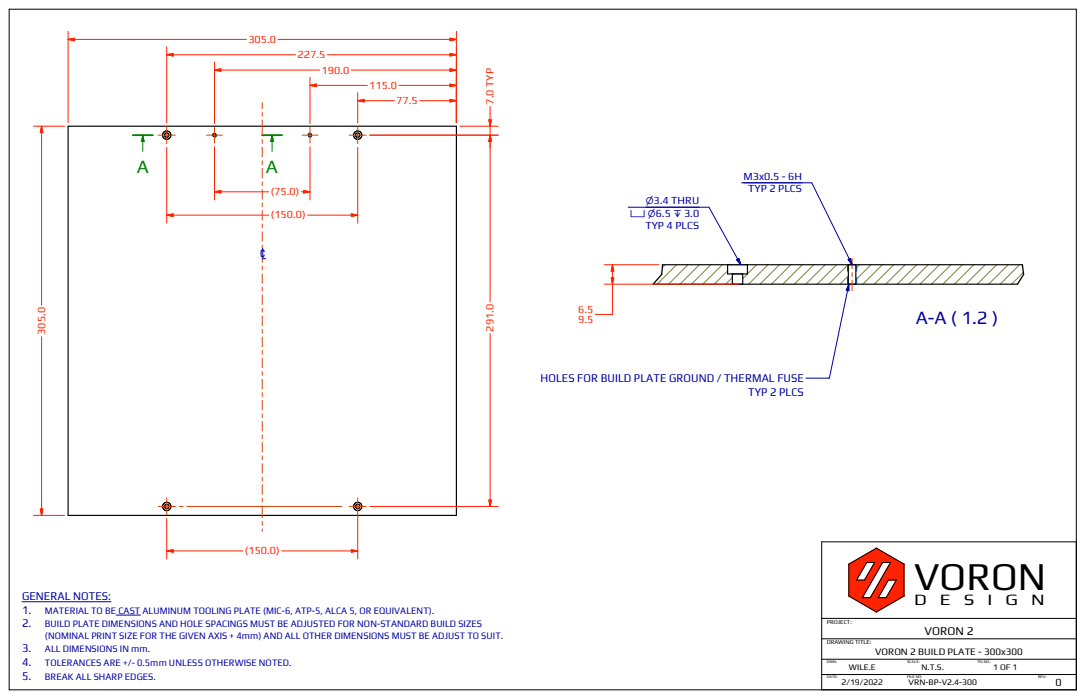
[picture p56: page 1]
VRN-BP-V2.4-300 DATE:; FILE NO:; PROJECT: DRAWING TITLE:; VORON 2; VORON 2 BUILD PLATE - 300x300 DWN:; SCALE:; PG NO: WILE.E; VORON; REV:; 190.0 291.0 7.0 TYP; TYP 2 PLCS; n3.4 THRU vn6.5 x 3.0 TYP 4 PLCS; M3x0.5 - 6H (75.0) TYP 2 PLCS

HOLES FOR BUILD PLATE GROUND / THERMAL FUSE

GENERAL NOTES:
1. MATERIAL TO BE CAST ALUMINUM TOOLING PLATE (MIC-6, ATP-5, ALCA 5, OR EQUIVALENT).
2. BUILD PLATE DIMENSIONS AND HOLE SPACINGS MUST BE ADJUSTED FOR NON-STANDARD BUILD SIZES
(NOMINAL PRINT SIZE FOR THE GIVEN AXIS + 4mm) AND ALL OTHER DIMENSIONS MUST BE ADJUST TO SUIT.
3. ALL DIMENSIONS IN mm.
4. TOLERANCES ARE +/- 0.5mm UNLESS OTHERWISE NOTED.
5. BREAK ALL SHARP EDGES.

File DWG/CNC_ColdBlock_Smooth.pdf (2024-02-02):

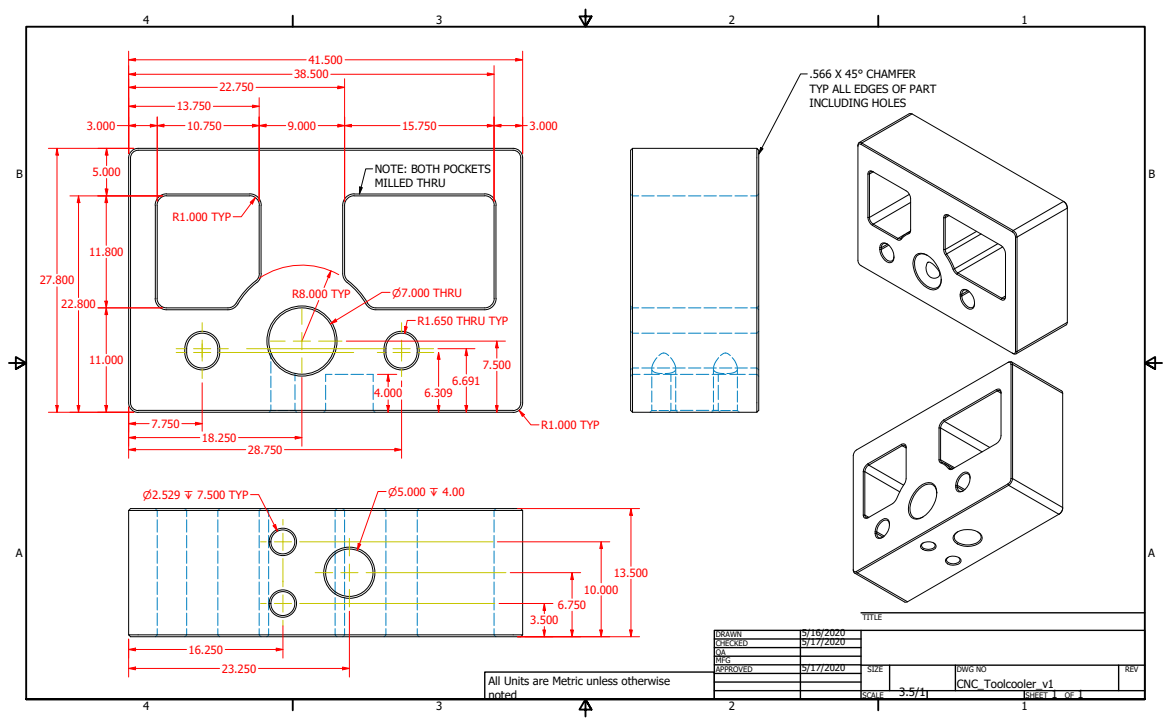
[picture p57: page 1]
SHEET 1 OF 1; R8.000 TYP; R1.000 TYP; R1.650 THRU TYP

.566 X 45° CHAMFER
TYP ALL EDGES OF PART
INCLUDING HOLES

NOTE: BOTH POCKETS
MILLED THRU

DRAWN | 5/16/2020
CHECKED | 5/17/2020
QA
MFG
APPROVED | 5/17/2020 | SIZE | DWG NO CNC_Toolcooler_v1 | REV

All Units are Metric unless otherwise
noted

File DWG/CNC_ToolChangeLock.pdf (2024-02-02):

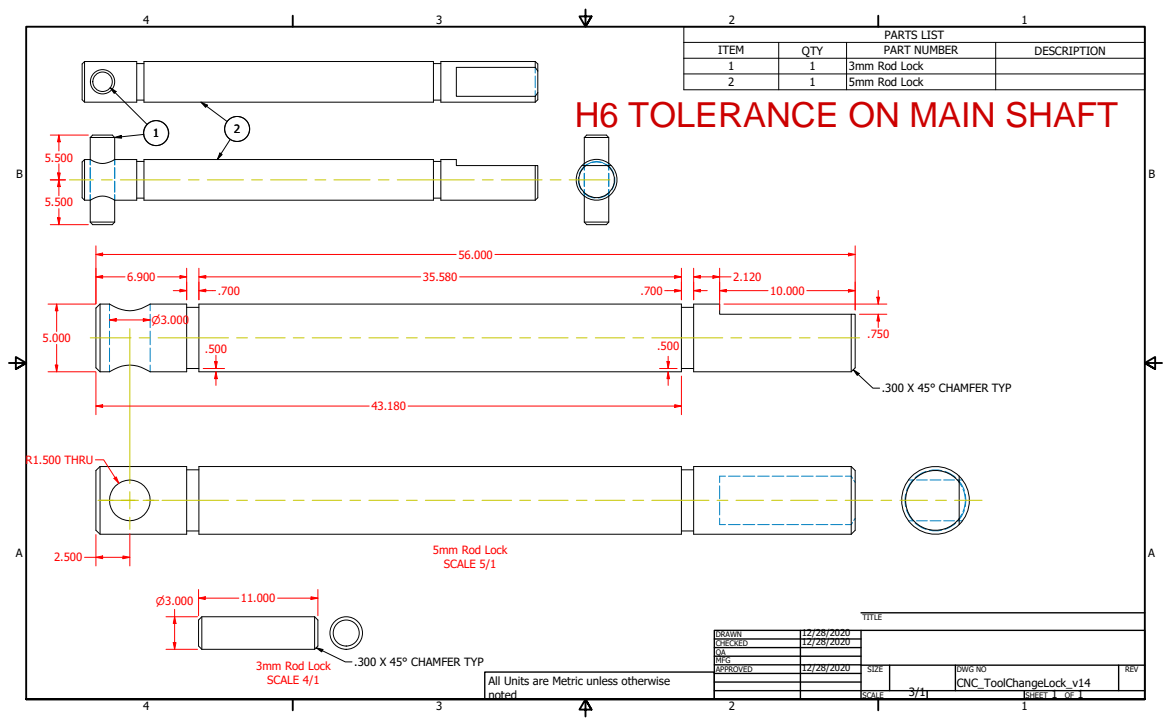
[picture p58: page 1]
3mm Rod Lock SCALE 4/1; 5mm Rod Lock SCALE 5/1; SHEET 1 OF 1; .300 X 45° CHAMFER TYP; R1.500 THRU

PARTS LIST

ITEM | QTY | PART NUMBER | DESCRIPTION
1 | 1 | 3mm Rod Lock
2 | 1 | 5mm Rod Lock

DRAWN | 12/28/2020
CHECKED | 12/28/2020

MFG
APPROVED | 12/28/2020 | SIZE | DWG NO CNC_ToolChangeLock_v14 | REV

All Units are Metric unless otherwise
noted

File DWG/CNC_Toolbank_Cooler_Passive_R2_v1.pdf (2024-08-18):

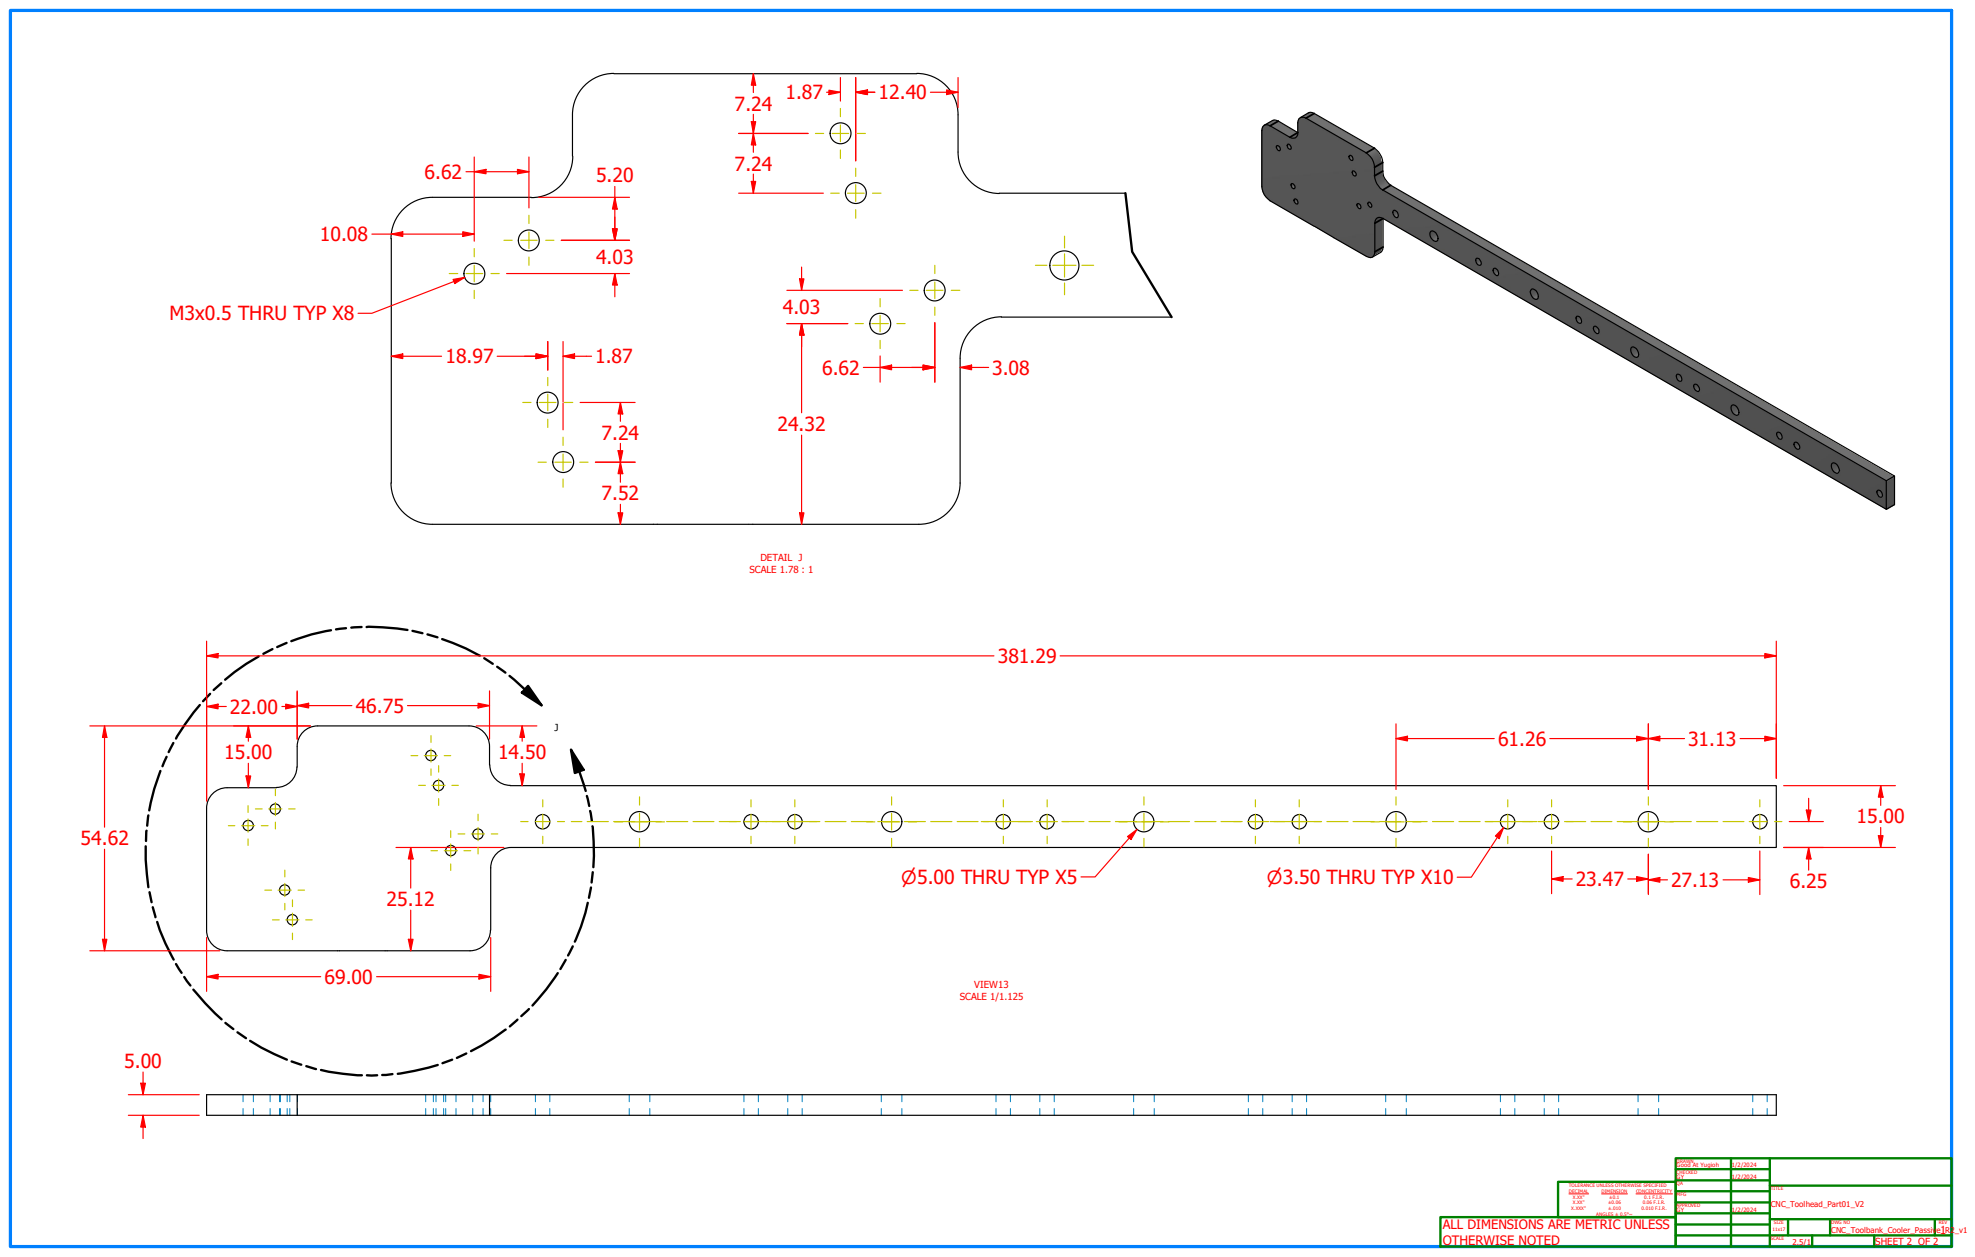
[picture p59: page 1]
SCALE 1/1.125; DETAIL J SCALE 1.78 : 1; ⌀5.00 THRU TYP X5; ⌀3.50 THRU TYP X10; M3x0.5 THRU TYP X8

DRAWN Good At Yugioh | 1/2/2024

CHECKED GY | 1/2/2024

TOLERANCE UNLESS OTHERWISE SPECIFIED DECIMAL DIMENSION CONCENTRICITY X.XX" ±0.1 X.XX" ±0.06 X.XXX" ±.010 ANGLES ± 0.5°~ | QA

APPROVED GY | 1/2/2024

ALL DIMENSIONS ARE METRIC UNLESS OTHERWISE NOTED | | | SIZE 11x17 | | DWG NO | REV 1

SCALE 2.5/1 | | SHEET 2 OF 2

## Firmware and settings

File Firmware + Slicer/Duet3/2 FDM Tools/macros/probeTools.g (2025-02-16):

; probeTools.G
; Original author: Haytham Bennani (H2B on Jubilee Discord - https://discord.gg/jubilee)
; This Macro is further tuned for use with Blackbox CE
; Firmware: RRF3.4.x and above
; This macro file utilizes the sexbolt Z switch by L.E.O.P.A.R.D and HartK to automatically set Z offsets on the Blackbox CE Toolchanger
; USAGE NOTES: 
;       - update the variables plateX and plateY as needed to reflect the actual position of your probe in your machine coordinates.
;       - ensure all your tools are at printing temperatures for best results
;       - ensure all your tool nozzles are clean from material and/or debris before probing, and its recommended to unload filaments from your tools before probing to ensure nothing flows out of the nozzle during the probing cycle
;       !! - ensure your definition for your doorknob probe (M558 line below) is correct for your setup !!
;
; DISCLAIMER: You bear full responsibility and accountability for using this script, and the author is not liable, nor responsible, nor accountable for any damage or misuse of this script.
;4.3mm above bed = Trigger point for sexbolt
;
;
;
;
; ----------------------------------------------- machine setup
; probe X and Y coordinates
var plateX = 266.2 ; Z Offset Probe location in X Direction (Determined with no tool active)
var plateY = 268.5 ; Z Offset Probe location in Y Direction (Determined with no tool active)

var staticOffset = 0.4 ;Static modifier based on unique trigger height -- More Negative = More Clearance
;------------------------------------------------ variable construction
var offsetX = 42   ; Predetermined Value of Carriage Mounted Z Switch compared to nozzle tip
var offsetY = -30  ; Predetermined Value of Carriage Mounted Z Switch compared to nozzle tip
var nozzleTipX = 0
var nozzleTipY = 0

set var.nozzleTipX = var.plateX + var.offsetX
set var.nozzleTipY = var.plateY + var.offsetY

; set acceleration values for P&T for smoother movement
M204 T4000 P4000
; instantaneous velocity change limits for smoother movement
M566 X400 Y400 P1
; re-define doorknob probe in case it is missing
M558 K1 P8 C"^io5.in" F200 H50
; placeholder for default Z endstop definition
;M558 P5 C"zstop" H10 A5 T42000 S0.02 F200
; disable any mesh compensation applied to the machine
M561

; ----------------------------------------------- calculation variables
; endstop trigger machine position
var endstopPoint = 0
; endstop doorknob trigger machine position
var probePoint = 0
; final tool offset variables
var t0_offset = 0
var t1_offset = 0

; ----------------------------------------------- probing sequence
echo "***** Probing endstop to doorknob trigger height difference.."
; unload tools (in case we've left anything on the carriage)
T-1
; drop bed slightly and move to probe point
G91 G1 Z5 G90
G90 G1 X{var.plateX} F6000
G90 G1 Y{var.plateY} F6000
;probe with doorknob probe (K1)
G30 S-1 K1
; save trigger position
set var.probePoint = move.axes[2].machinePosition
; drop bed slightly, and re-probe with default Z endstop (K0)
G91 G1 Z3 G90
G30 S-1 K0
; save trigger position
set var.endstopPoint = move.axes[2].machinePosition
; calculate trigger height difference between doorknob and endstop
var offsetProbe =  var.endstopPoint - var.probePoint
; drop bed before next operation for clearance
G91 G1 Z5 G90

; ----------------------------------------------- Tool 0
echo "***** Measuring T0 offset.."
T0
; drop bed slightly and move to probe point
G91 G1 Z5 G90
G90 G1 X{var.nozzleTipX} Y{var.nozzleTipY} F6000
; probe tool with doorknob probe (K1)
G30 S-1 K1
; capture trigger height and calulate initial offset (without endstop trigger height adjustment)
set var.t0_offset = move.axes[2].machinePosition - var.probePoint 
; apply endstop trigger height adjustment for final offset value
set var.t0_offset = var.offsetProbe - var.t0_offset + var.staticOffset ; final value compensates for switch overtravel
; drop bed before next operation for clearance
G91 G1 Z5 G90

; ----------------------------------------------- Tool 1
echo "***** Measuring T1 offset.."
T1
; drop bed slightly and move to probe point
G91 G1 Z5 G90
G90 G1 X{var.nozzleTipX} Y{var.nozzleTipY} F6000
; probe tool with doorknob probe (K1)
G30 S-1 K1
; capture trigger height and calulate initial offset (without endstop trigger height adjustment)
set var.t1_offset = move.axes[2].machinePosition - var.probePoint
; apply endstop trigger height adjustment for final offset value
set var.t1_offset = var.offsetProbe - var.t1_offset + var.staticOffset ; final value compensates for switch overtravel
; drop bed before next operation for clearance
G91 G1 Z5 G90



; ----------------------------------------------- Re-measure endstop trigger height
; unload tools
T-1
; drop bed slightly and move to probe point
G91 G1 Z5 G90
G90 G1 X{var.plateX} Y{var.plateY} F6000
echo "***** Confirming trigger height difference.."
; drop bed slightly, and probe with doorknob probe (K1)
G91 G1 Z5 G90
G30 S-1 K1
; save trigger position
set var.probePoint = move.axes[2].machinePosition
; drop bed slightly, and re-probe with default Z endstop (K0)
G91 G1 Z5 G90
G30 S-1 K0
; save trigger position
set var.endstopPoint = move.axes[2].machinePosition
; calculate trigger height difference between doorknob and endstop
var offsetProbe2 =  var.endstopPoint - var.probePoint
; drop bed before next operation for clearance
G91 G1 Z5 G90
; send carriage to origin point (0,0)
G0 X0 Y0 F6000

; ----------------------------------------------- Probe Report
echo "----------------------------------------------------------------"
echo "                    Calibration setup data"
echo "Initial probe offset: " ^ var.offsetProbe
echo "Final probe offset: " ^ var.offsetProbe2
echo "----------------------------------------------------------------"
echo "                   Calculated tool offsets"
echo "T0 Z offset: " ^ var.t0_offset
echo "T1 Z offset: " ^ var.t1_offset

echo "----------------------------------------------------------------"
echo "                 G10 commands for config file"
echo "G10 P0 Z" ^ var.t0_offset
echo "G10 P1 Z" ^ var.t1_offset

echo "----------------------------------------------------------------"
; ----------------------------------------------- Apply offsets to tools
G10 P0 Z{var.t0_offset}
G10 P1 Z{var.t1_offset}

; ----------------------------------------------- Prompt user to save offsets to config
echo "Probing completed: offsets are applied to current tools."
echo "Please save G10 commands to config.g for persistence if needed."

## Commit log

2024-02-02 Blackbox CE Release - Initial
    Initital
    [Acrylic_Front_Door.dxf, CNC_Acrylic_Floor_Left_Basic.dxf, CNC_Acrylic_Floor_Left_PanelDue7i.dxf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]
2024-02-02 BOM Update
    Removed Empty Pages
2024-02-11 Initial Firmware + Wiring
    [disableLockMotor.g, probeTools.g]
2024-02-15 Update Print_SexBolt_Housing_V2 v2_QTY_1.stl
    [Print_SexBolt_Housing_V2 v2_QTY_1.stl]
2024-03-30 Config Update
    [probeTools.g]
2024-04-27 Guide Updates
    [Print_Standard_Lock_Motor_Installation_Tool_(1.7).stl]
2024-08-18 V1.1 Release
    V1.1 Release
    [CNC_Acrylic_Floor_Left_PanelDue7i.dxf, CNC_Acrylic_Floor_Right_Basic.dxf, CNC_Acrylic_Floor_Right_PanelDue7i.dxf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]
2025-02-15 V1.1 R1 Release
    [CNC_Acrylic_Floor_Right_Basic.dxf, CNC_Acrylic_Floor_Right_PanelDue7i.dxf, Print_ACSwHouse_CE v2_QTY_1.stl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]
2025-02-15 Update Blackbox CE - Wiring.pdf
2025-02-16 Update Firmware
    [probeTools.g]
